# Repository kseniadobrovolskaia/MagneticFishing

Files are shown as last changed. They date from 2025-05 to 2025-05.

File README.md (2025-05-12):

# Аттракцион "Магнитная рыбалка"

> [!NOTE]
> Аттракцион сделан по мотивам известных призовых автоматов [кран-машина](https://ru.wikipedia.org/wiki/%D0%9A%D1%80%D0%B0%D0%BD_(%D0%B8%D0%B3%D1%80%D0%BE%D0%B2%D0%BE%D0%B9_%D0%B0%D0%B2%D1%82%D0%BE%D0%BC%D0%B0%D1%82)) в рамках курса ППП (проектирование, прототипирование, производство) на *Физтех.Фабрике*. :smile:

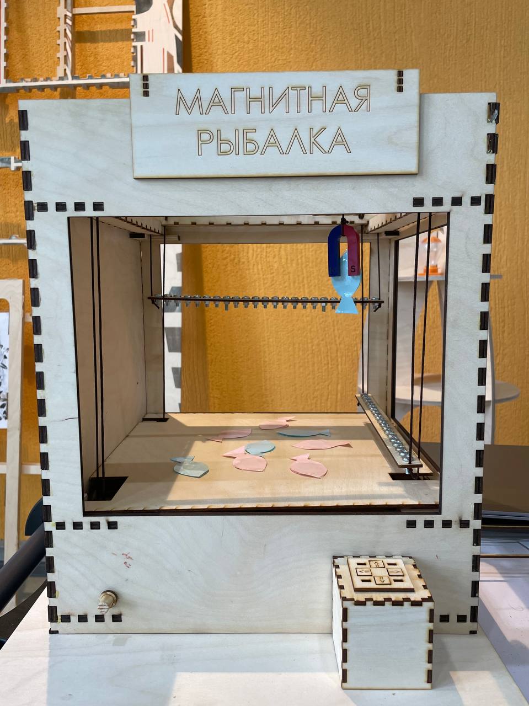
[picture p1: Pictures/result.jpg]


## Содержание

[1. Проектирование](#1)

Три+ версий аттракциона

[2. Прототипирование](#2)

Разработка в *SolidWorks* -> *CorelDraw*

[3. Производство](#3)

Лазерные станки

[4. Работа аттракциона](#4)

 -----------------------------------------------------------------------------

 ## Проектирование

Это было самым долгим и сложным процессом в работе над проектом. Было много вариантов системы, расскажем о наиболее отличающихся друг от друга.

### Вариант 1

В первом варианте аттракциона было рассчитано, что движение управляющего механизма по осям x и y будет происходить в одну сторону за счет тяги сервоприводов, а в другую за счет силы тяжести:



Проведя моделирование такой системы, было выяснено, что трение слишком велико и требуется добавить грузы. 

### Вариант 2

Тогда можно было отказаться от наклонного механизма и оставить одно колесо и рельсу для каждой оси:



Моделирование такого варианта тоже закончилось плохо и мы добавили вторые колеса и рельсы:

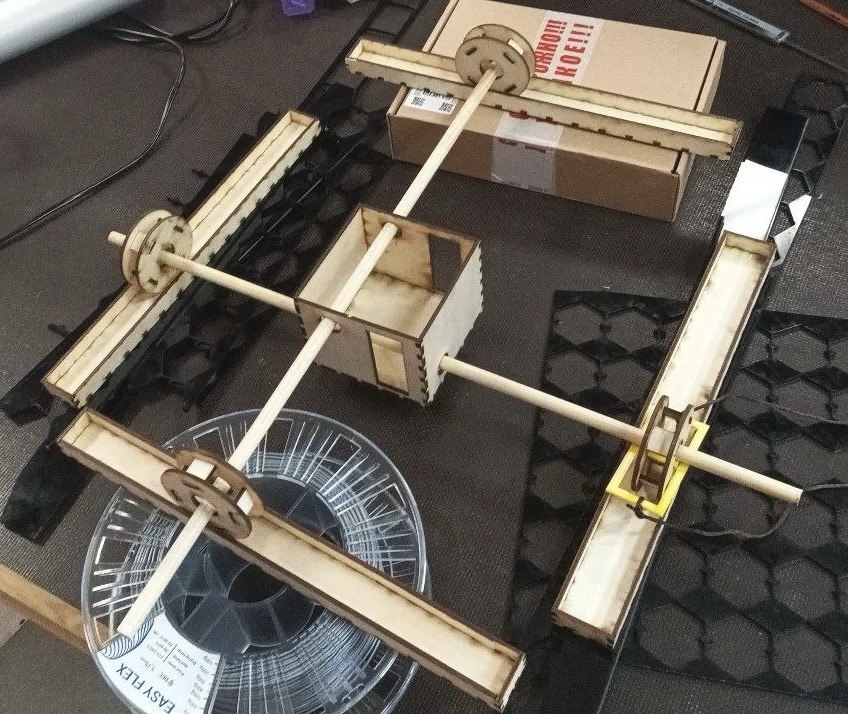
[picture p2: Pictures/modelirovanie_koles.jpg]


Но возникла проблема в другом: система с грузом и одним серво была несимметрична, поэтому попытка поехать заканчивалась перекошенным и вставшим механизмом. Эта проблема проиллюстрирована на видео. Если тянуть только за одно колесо, появляется крутящий момент и управляющий механизм разворачивается. 

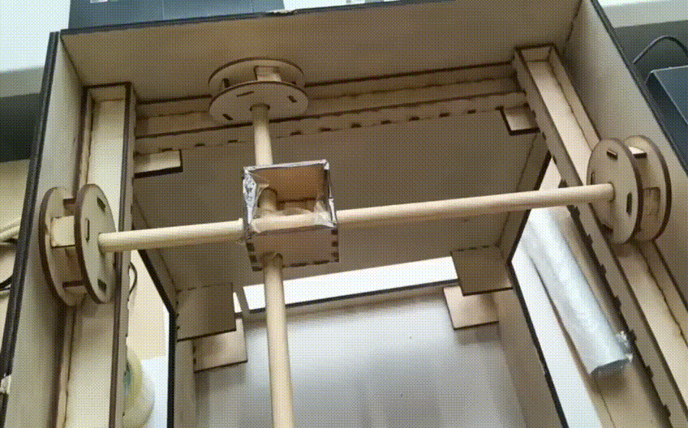
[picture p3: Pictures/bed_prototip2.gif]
  

### Вариант 3

Было решено добиться симметрии, установив серво внизу и распределив его силу на оба колеса с помощью шестеренок:



Шестеренки вырезали из дерева:

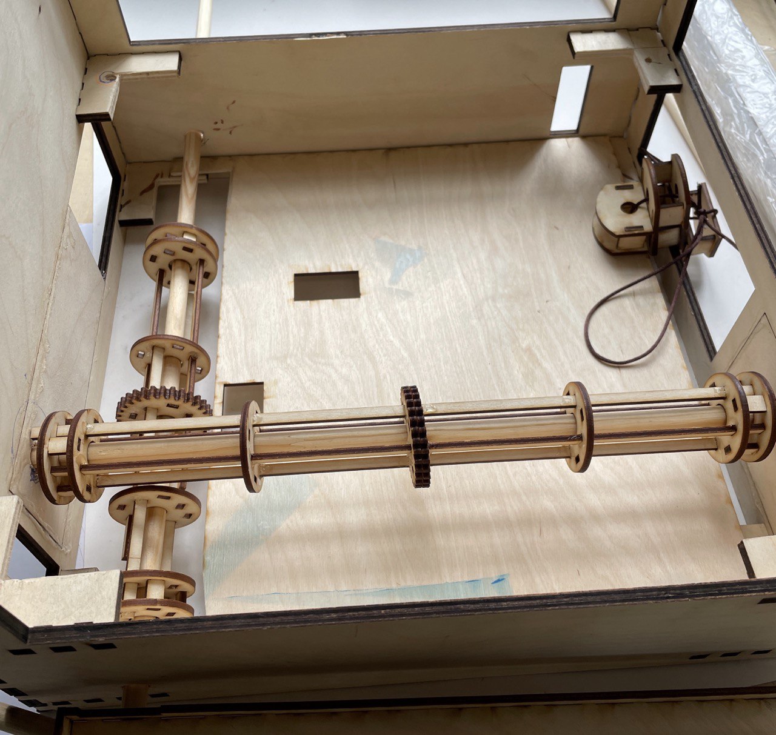
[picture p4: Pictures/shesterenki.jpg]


Этот механизм уже заработал:

  

Но мы поняли, что колеса почти не вращаются, поэтому их можно заменить на обычные плоские наконечники для палок:

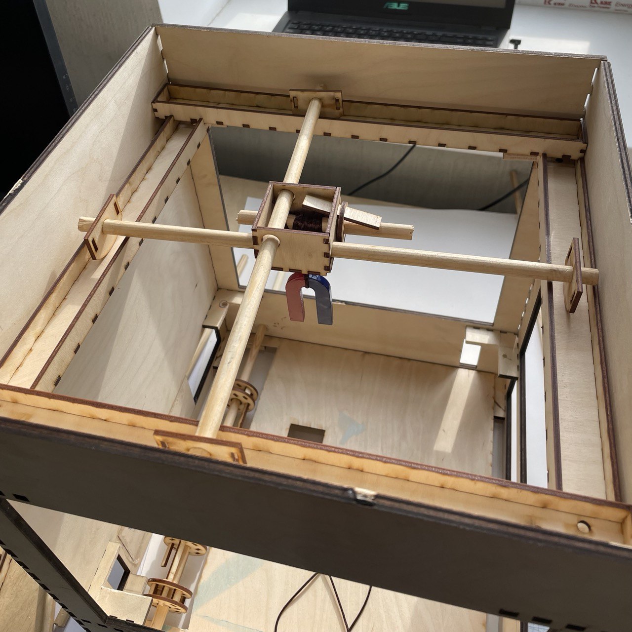
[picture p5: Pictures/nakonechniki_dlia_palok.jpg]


Это стало окончательным вариантом движущегося механизма.
 
 -----------------------------------------------------------------------------
 
 ## Прототипирование

Использовалась CAD/CAM система *SolidWorks*. В ней были разработаны главные компоненты аттракциона:

1. [**Корпус**](https://github.com/kseniadobrovolskaia/MagneticFishing/blob/main/SolidWorksFiles/корпус.SLDPRT)

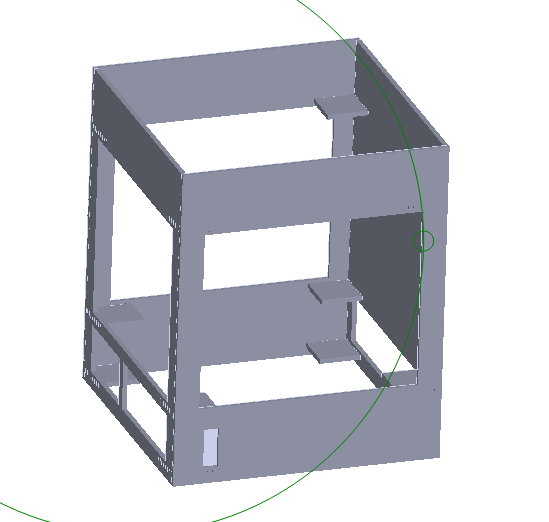
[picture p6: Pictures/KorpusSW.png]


2. [**Шестеренки**](https://github.com/kseniadobrovolskaia/MagneticFishing/blob/main/SolidWorksFiles/шестеренка.SLDPRT) 

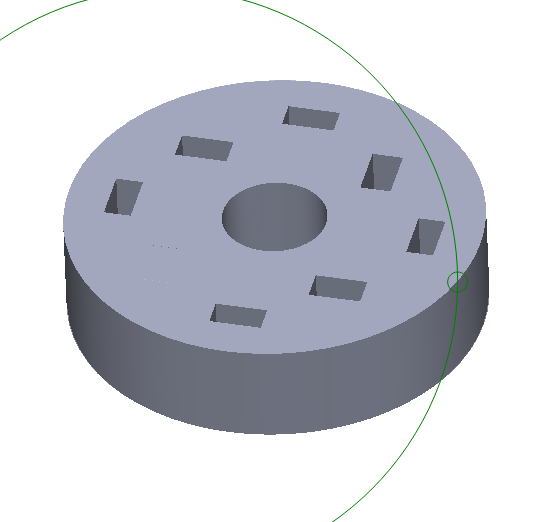
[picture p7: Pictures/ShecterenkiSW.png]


3. [**Наконечники для палок**](https://github.com/kseniadobrovolskaia/MagneticFishing/blob/main/SolidWorksFiles/таскалки.SLDPRT) 

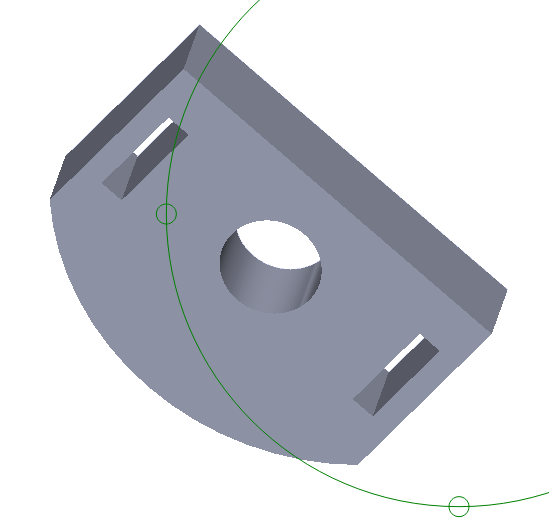
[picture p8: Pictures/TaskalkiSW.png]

 
4. [**Удочка**](https://github.com/kseniadobrovolskaia/MagneticFishing/blob/main/SolidWorksFiles/удочка.SLDPRT) 

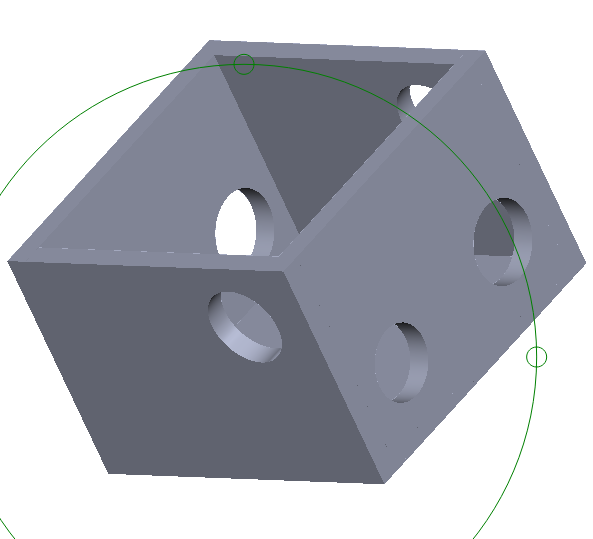
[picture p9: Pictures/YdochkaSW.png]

 
5. [**Джостик для кнопок**](https://github.com/kseniadobrovolskaia/MagneticFishing/blob/main/SolidWorksFiles/джостик_с_кнопками.SLDPRT) 

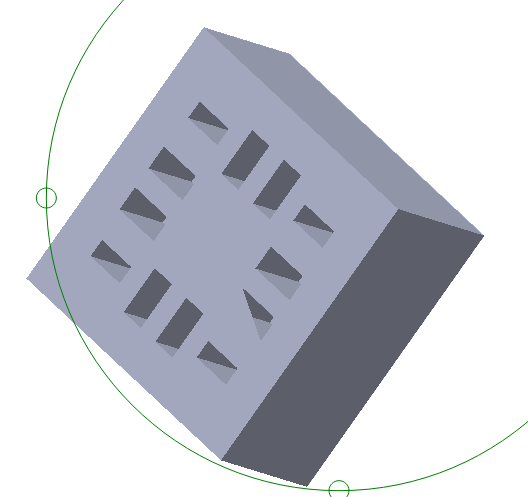
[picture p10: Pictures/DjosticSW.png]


Далее плоскости всех объектов были импортированы в *DXF* формат и открыты в системе *CorelDraw* для отправки на печать. В этой же системе были разработаны остальные простые детали, не требующие соединений шип-паз.

 -----------------------------------------------------------------------------

 ## Производство

Для печати корпуса была использована деревянная фанера 6 мм и большой лазерный станок:

  

Для остальных комплектующих - фанера 3 мм и маленький лазерный станок:

  

Для управления механизмом была использована плата микроконтроллера Arduino MEGA. К ней были припаяны кнопки, реализующие [логику сервоприводов](https://github.com/kseniadobrovolskaia/MagneticFishing/blob/main/ServoProg/sketch_servo.ino) для управления движением магнита по осям x и y:



Сервоприводы были закреплены в дне корпуса:

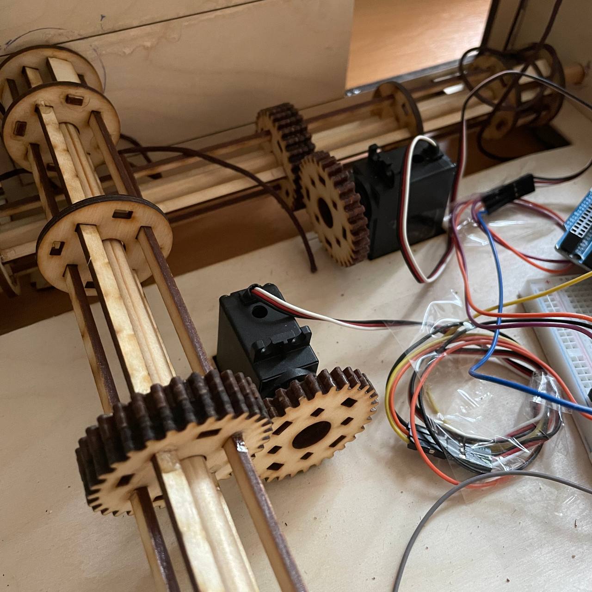
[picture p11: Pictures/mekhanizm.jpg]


Кнопки были вставлены в джостик:

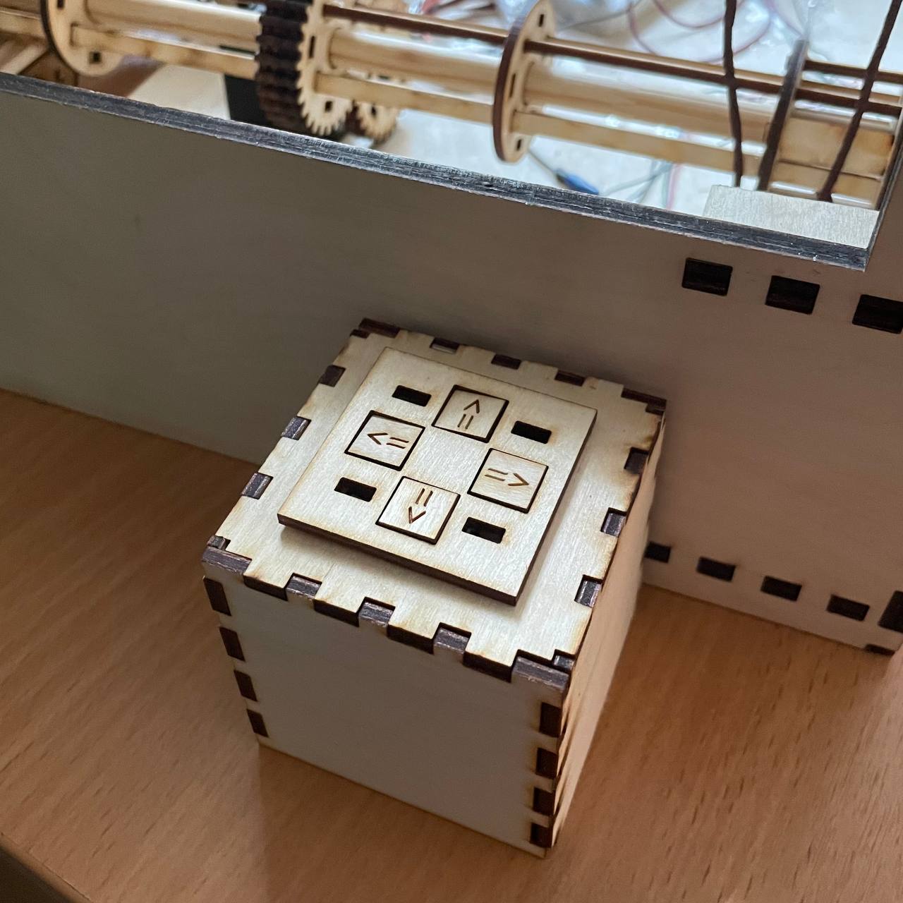
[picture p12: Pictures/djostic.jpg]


Колеса соединены нитками с катушкой вращающего механизма с одной стороны и с утяжеляющей конструкцией, за счет которой происходит движение в обратном направлении.

  

В итоге получилась такая конструкция:

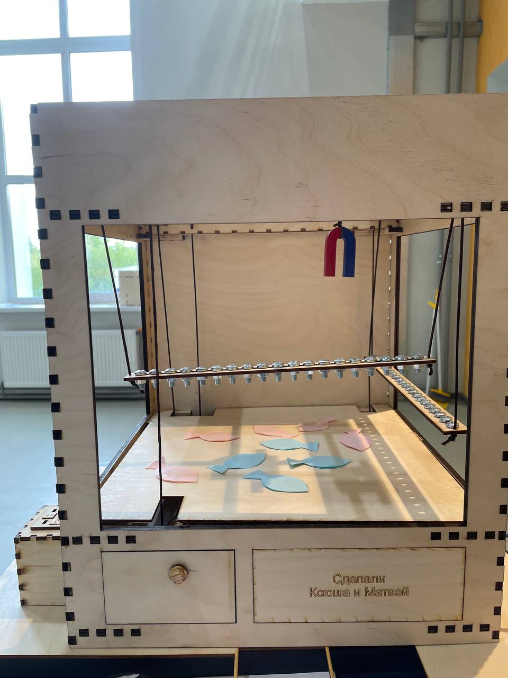
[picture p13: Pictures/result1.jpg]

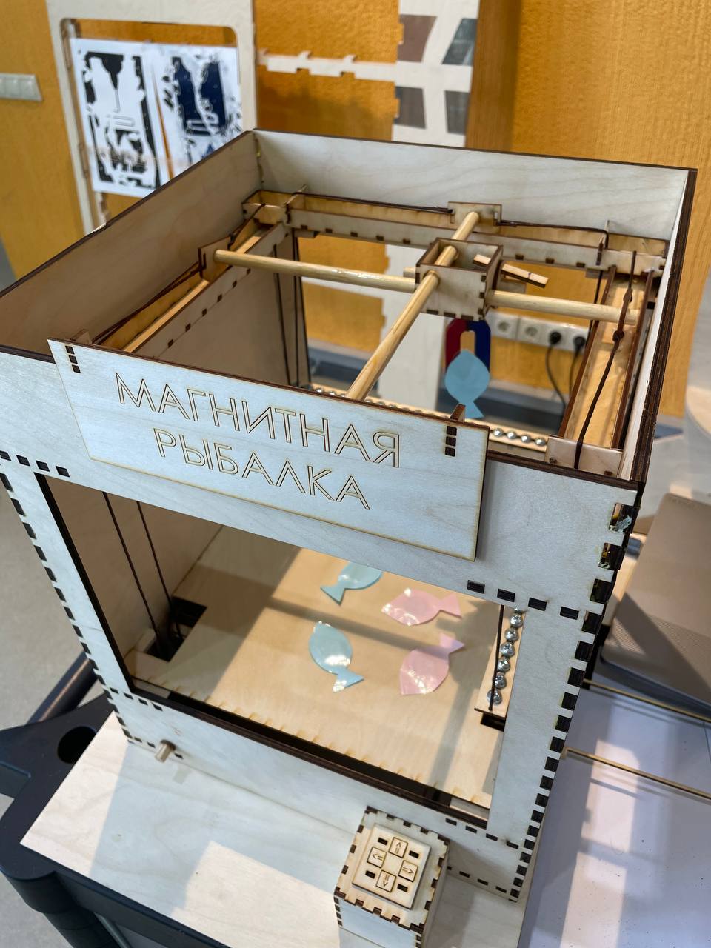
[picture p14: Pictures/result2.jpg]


 -----------------------------------------------------------------------------

 ## Работа аттракциона

> [!IMPORTANT]
> Магнит не является электрическим, а выдача призов происходит не как в известном автомате, потому что аттракцион задуман, как имитация настоящей рыбалки, где тащить рыбу нужно самостоятельно :smile:



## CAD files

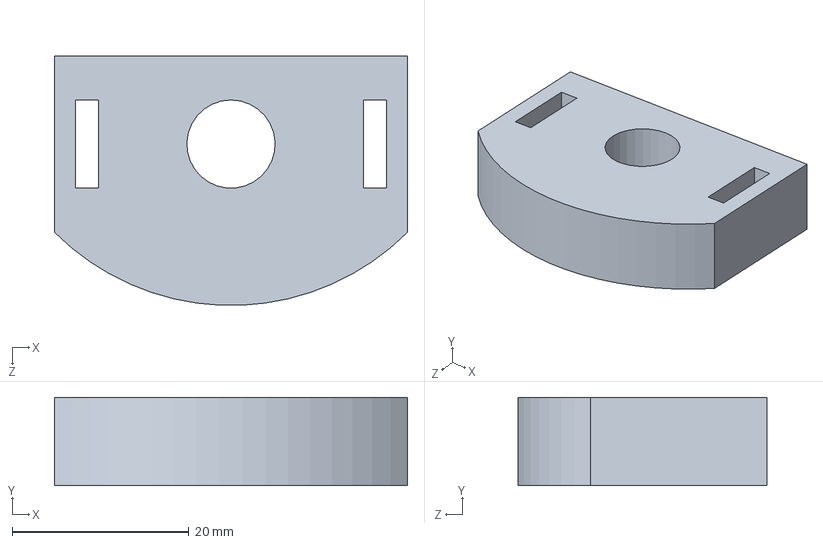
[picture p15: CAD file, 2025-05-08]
SolidWorksFiles/таскалки.SLDPRT
40.0 x 10.0 x 28.3 mm

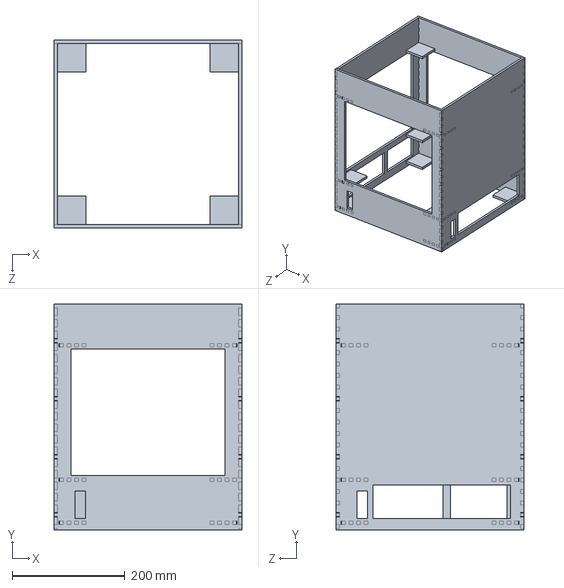
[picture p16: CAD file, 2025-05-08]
SolidWorksFiles/корпус.SLDPRT
332.0 x 400.0 x 332.0 mm

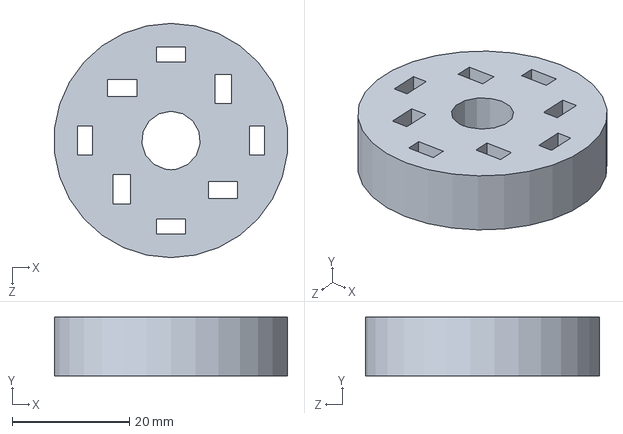
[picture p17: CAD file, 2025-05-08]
SolidWorksFiles/шестеренка.SLDPRT
39.8 x 10.0 x 40.0 mm

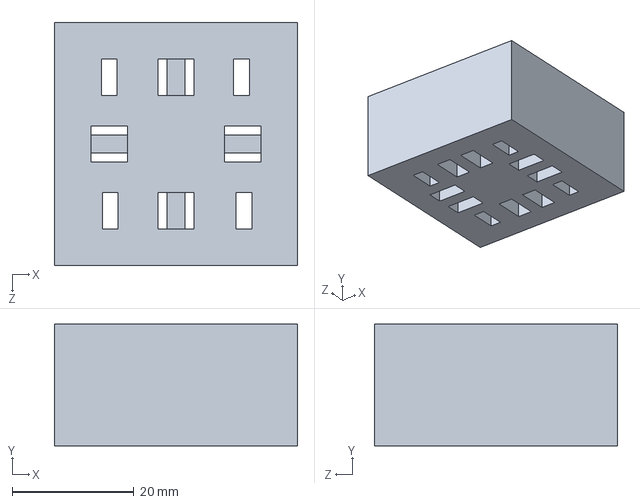
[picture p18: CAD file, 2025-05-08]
SolidWorksFiles/джостик_с_кнопками.SLDPRT
40.0 x 20.0 x 40.0 mm

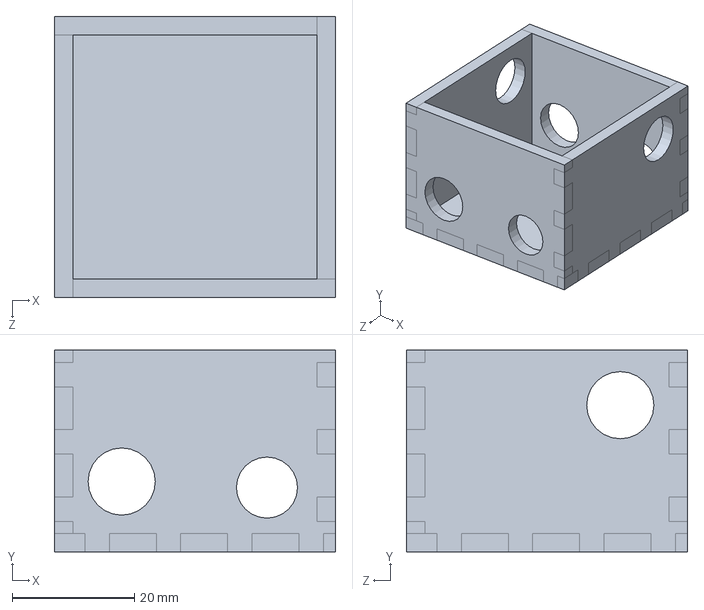
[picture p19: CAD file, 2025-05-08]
SolidWorksFiles/удочка.SLDPRT
46.0 x 33.0 x 46.0 mm

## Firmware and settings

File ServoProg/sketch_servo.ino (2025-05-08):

#include <Servo.h>

const int ForwardSpeed = 90; // < 90!
const int BackwardSpeed = 90; // < 90!
const unsigned long DebounceDelay = 50;

struct PinnedServo {
  int servoPin;
  int forwardButtonPin;
  int reverseButtonPin;
  Servo servo;
  bool isRotating;
  unsigned long lastDebounceTime;

  void setup(int servoPin_, int forwardButtonPin_, int reverseButtonPin_) {
    servoPin = servoPin_;
    forwardButtonPin = forwardButtonPin_;
    reverseButtonPin = reverseButtonPin_;

    servo.attach(servoPin);
    pinMode(forwardButtonPin, INPUT_PULLUP);
    pinMode(reverseButtonPin, INPUT_PULLUP);
    servo.detach();

    isRotating = false;
    lastDebounceTime = 0;
  }

  void rotateForward() {
    servo.attach(servoPin);
    servo.write(90 + ForwardSpeed); // Full counterclockwise rotation
  }

  void rotateReverse() {
    servo.attach(servoPin);
    servo.write(90 - BackwardSpeed);   // Full clockwise rotation
  }

  void stop() {
    servo.detach();
  }

  void update() {
    int forwardReading = digitalRead(forwardButtonPin);
    int reverseReading = digitalRead(reverseButtonPin);
    
    // Debounce check
    if ((millis() - lastDebounceTime) > DebounceDelay) {
      if (forwardReading == LOW && !isRotating) { // Forward button pressed
        Serial.println("Forward button pressed!");
        rotateForward();
        isRotating = true;
      } else if (reverseReading == LOW && !isRotating) { // Reverse button pressed
        Serial.println("Reverse button pressed!");
        rotateReverse();
        isRotating = true;
      } else if ((forwardReading == HIGH || reverseReading == HIGH) && isRotating) {
        Serial.println("Button released!");
        stop();
        isRotating = false;
      }
      lastDebounceTime = millis();
    }
  }
};

PinnedServo servoX;
PinnedServo servoY;

void setup() {
  Serial.begin(9600);
  servoX.setup(6, 10, 11);
  servoX.stop();

  servoY.setup(7, 12, 13);
  servoY.stop();
}

void loop() {
  // Serial.println(digitalRead(10));
  servoX.update();
  servoY.update();
}
